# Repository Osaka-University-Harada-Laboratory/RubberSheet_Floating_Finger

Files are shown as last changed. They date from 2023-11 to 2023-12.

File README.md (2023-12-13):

# オープンソース版フローティングフィンガー（近接覚センサTK-01使用）

## 概要
- 3Dビジョンレスばら積みピッキングや突き指防止機能を持つ柔軟機構・センシングユニット．

- 具体的な組立手順はYouTubeに公開 ---> https://youtu.be/J7uZkjt3QmM

- 第24回計測自動制御学会システムインテグレーション部門講演会(SI2023)において発表．<br>
発表タイトル：**柔軟膜を用いたオープンソースなフローティングフィンガー機構**

<!-- ![Overview](/images/SI2023_fig_overview.png) -->


## パーツ
- ipt：inventor向けCADデータ (.ipt, .iam)
- step：STEPファイル (.stp)
- 組み立て後のデータ：RSFF_assembly_1_v3_clearance

### 近接覚センサ：TK-01
- 株式会社Thinker製の近接覚センサ"TK-01"を使用
- 以下から見積もり・購入が可能

  https://www.thinker-robotics.co.jp/contact

### センサケース
- 該当CADファイル：RSFF_cover_1_v3_clearance\
- 3Dプリンタで製作

<br><br>
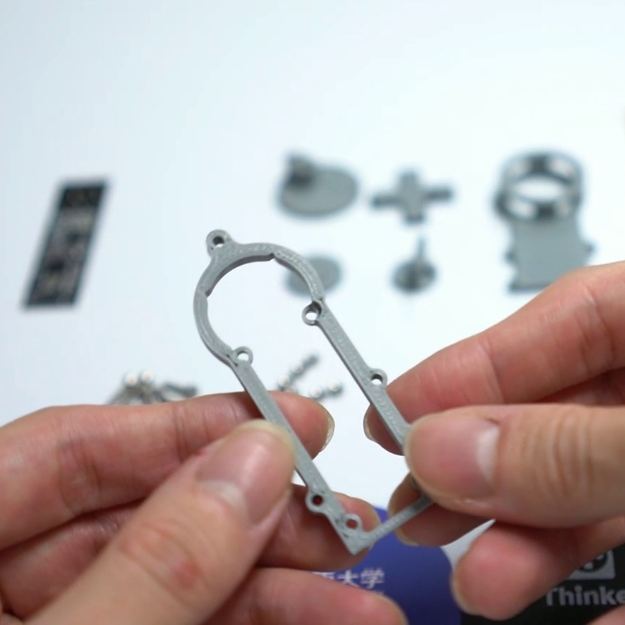
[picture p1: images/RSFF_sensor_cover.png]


### センサカバー
- 該当CADファイル：RSFF_cover_2_v2_clearance\
- 3Dプリンタで製作

<br><br>
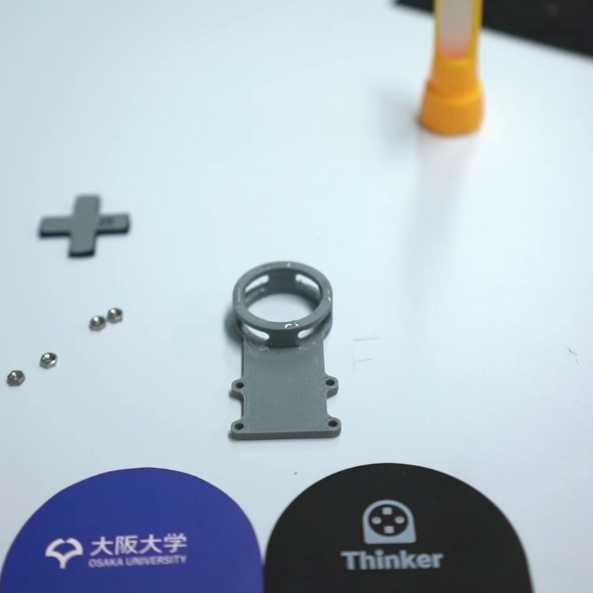
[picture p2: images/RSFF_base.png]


### 柔軟膜
- 該当CADファイル：RubberSheet_1
- 材料：市販の飴ゴムシート　[購入先リンク](https://www.monotaro.com/g/01013365/?t.q=%E9%A3%B4%E3%82%B4%E3%83%A0%E3%82%B7%E3%83%BC%E3%83%88)\
- 作成方法：RubberSheet_1を3Dプリンターで印刷したパーツをもとに切り取る
<br><br>
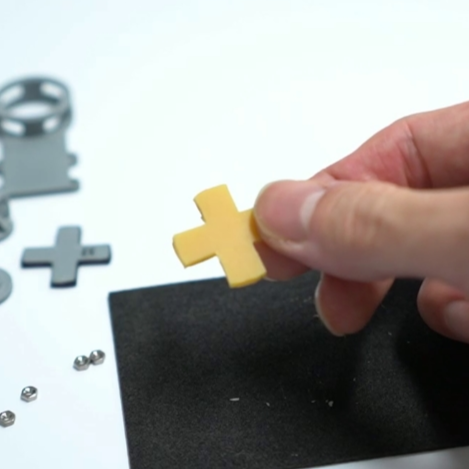
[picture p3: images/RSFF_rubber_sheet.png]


### 爪
- 該当CADファイル：RSFF_tip_metal_1\
- 素材：アルミニウム\
- 作成方法：meviyを利用し外注　[meviyリンク](https://meviy.misumi-ec.com/ja-jp/)
<br><br>


### 爪と柔軟膜の接続部分
- 該当CADファイル：RSFF_tip_mount_1\
- 作成方法：センサカバーと同じ
<br><br>
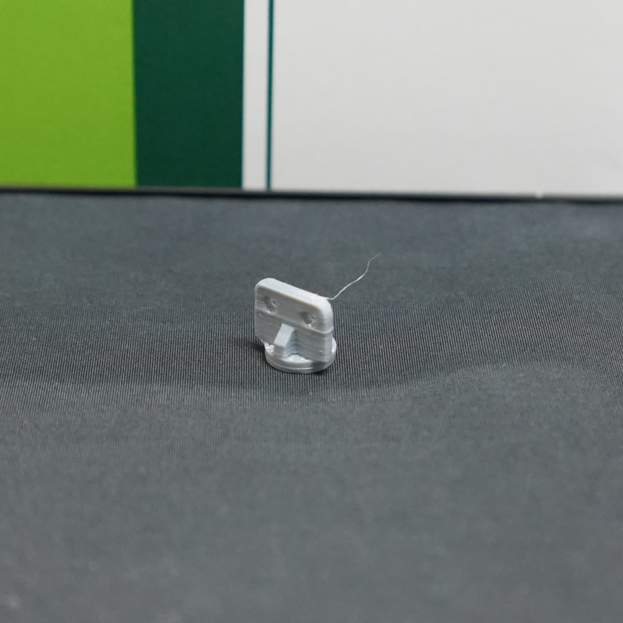
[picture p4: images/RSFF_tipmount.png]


### 反射板
- 該当CADファイル：RSFF_reflector_v2\
- 作成方法：センサカバーと同じ
<br><br>
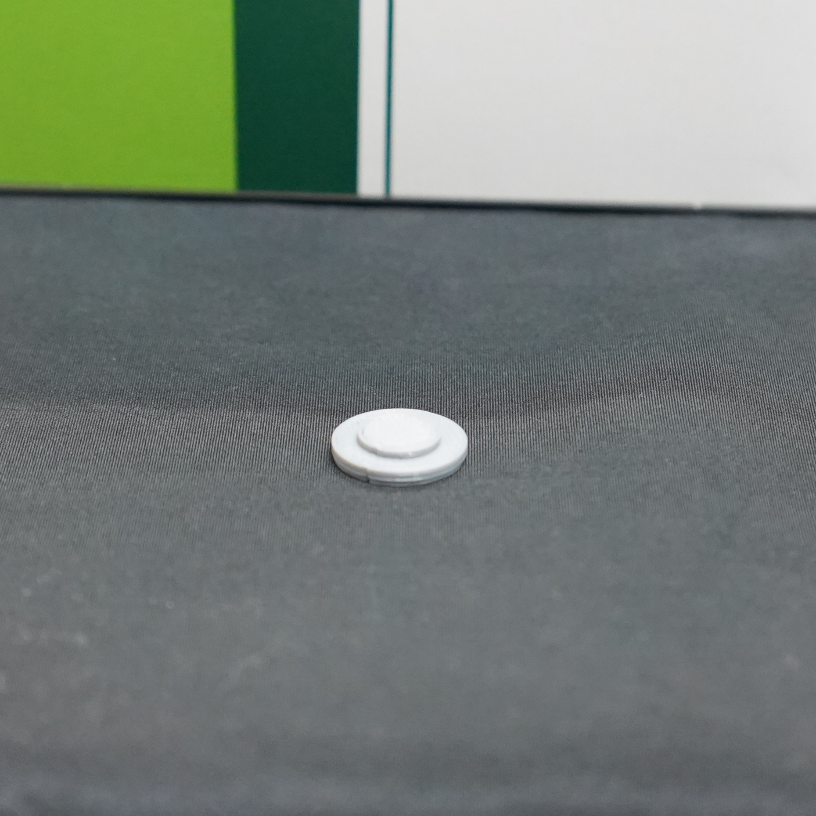
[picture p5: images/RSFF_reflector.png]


### COBOTTAの手先との接続部分
- 該当CADファイル：RSFF_mount_1_clearance, RSFF_mount_1_clearance_MIR1\
- 作成方法：センサカバーと同じ
<br><br>
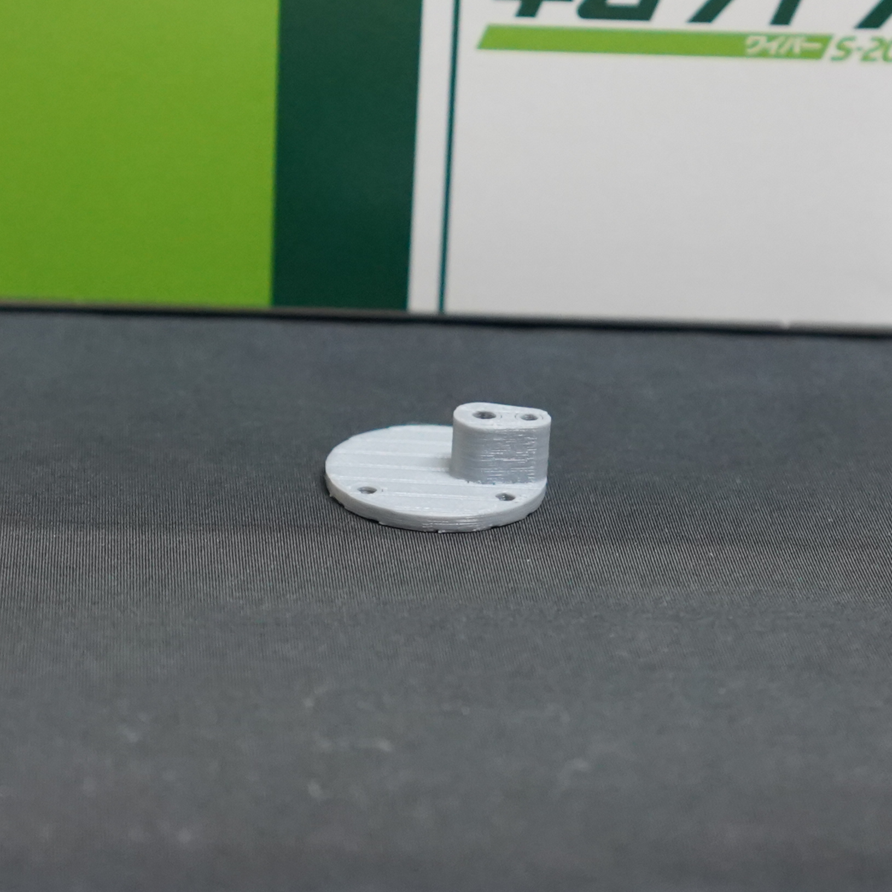
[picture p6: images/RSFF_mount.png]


## 道具・細かい部品
- ハサミ
- ボルト(M2×8：6個，M2×10：5個)
- ナット(M2)
- 瞬間接着剤（アロンアルファ，他種の接着剤では接着力が減少する場合があるので注意）
- 白い紙
- 低反射黒インク（「黒色無双」相当品）[購入先リンク](https://www.amazon.co.jp/dp/B08JYK85HP/?m=A3NCQXDSLN8VX8)\
- 筆

### 使用実績のある3Dプリンタ

研究室では以下の2種類の3Dプリンターで作成した実績あり．

  1. **光造形式3Dプリンター (AGILISTA-3200)**
     - モデル材：AR-M2
     - サポート材：AR-S1
  1. **FDM式3Dプリンター (Zortrax M200 Plus)**
     - フィラメント：Z-ULTRAT (ABS系樹脂)

## 構造図

- 具体的な組立手順はこちら ---> https://youtu.be/J7uZkjt3QmM

<!-- ![組み立て](/images/SI2023_fig_CAD_2.png) -->
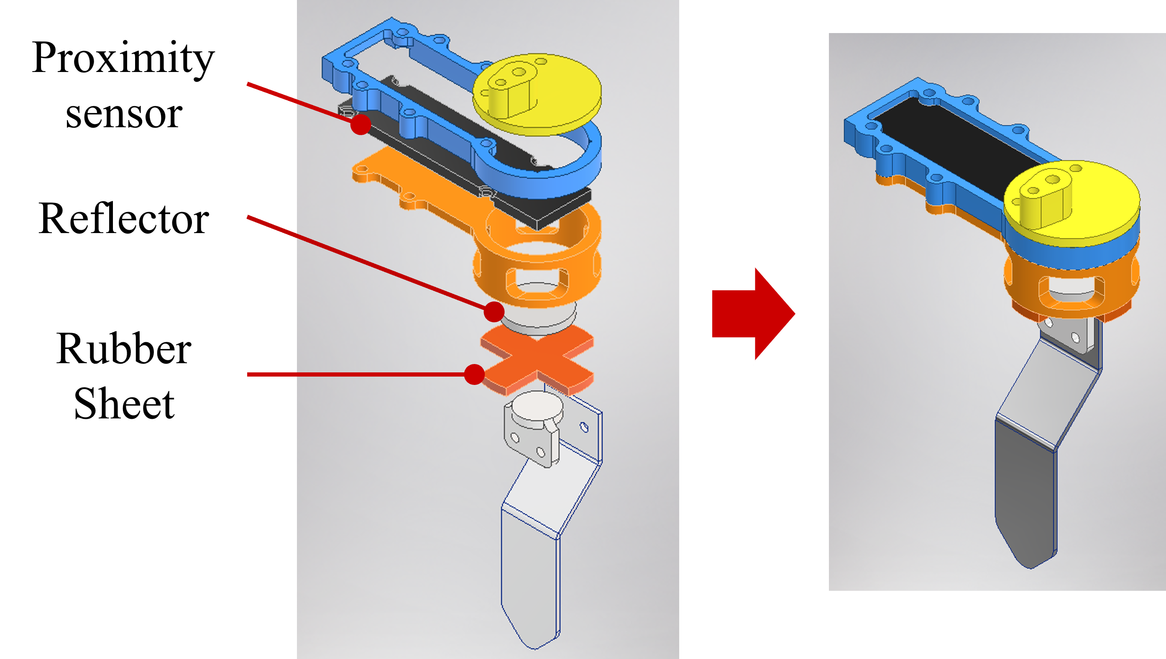
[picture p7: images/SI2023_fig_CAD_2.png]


## 備考
- センサカバーにはセンサ基板に対して約0.2mmのクリアランスを設けている．

## 謝辞
- 本研究は株式会社Thinkerとの共同研究の一環として実施された．

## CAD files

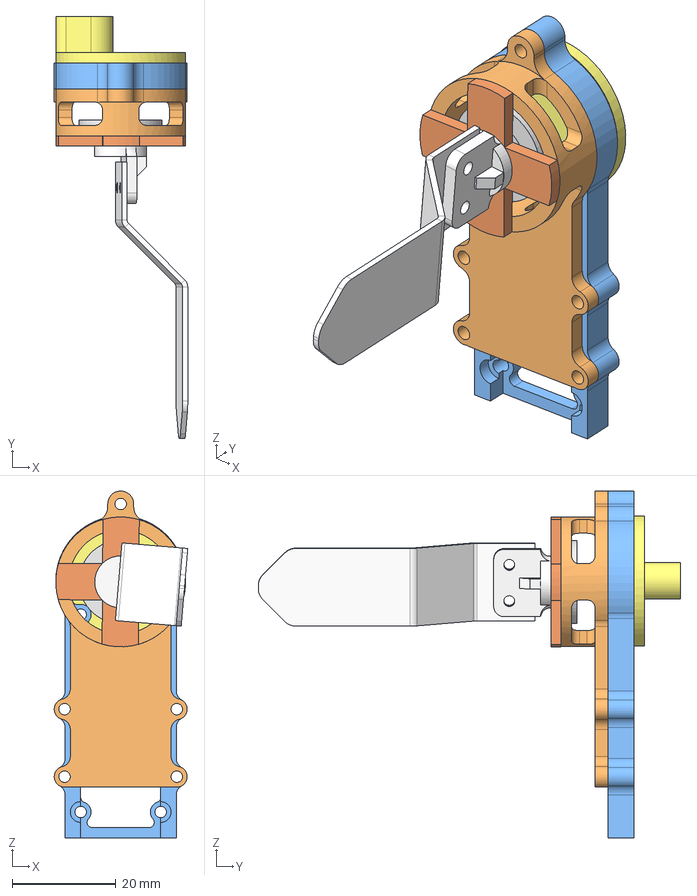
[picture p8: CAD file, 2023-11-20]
step/RSFF_assembly_1_v3_clearance.stp
25.7 x 81.3 x 66.8 mm
RSFF_cover_1_v3_clearance
RSFF_cover_2_v2_clearance
RSFF_tip_mount_1_clearance
RSFF_reflector_v2
RSFF_tip_mount_1
RubberSheet_1
RSFF_tip_metal_1

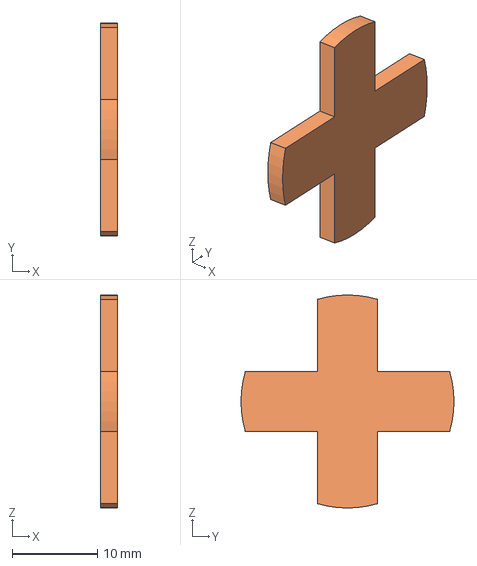
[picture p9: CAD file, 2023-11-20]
step/RubberSheet_1.stp
2.00 x 25.0 x 25.0 mm

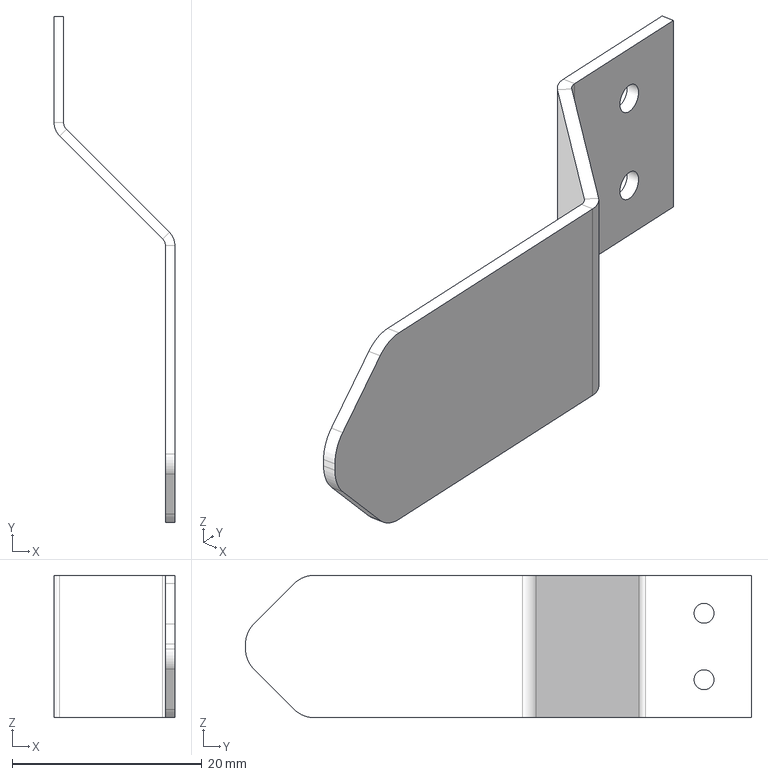
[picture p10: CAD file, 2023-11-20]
step/RSFF_tip_metal_1.stp
12.7 x 53.3 x 15.0 mm

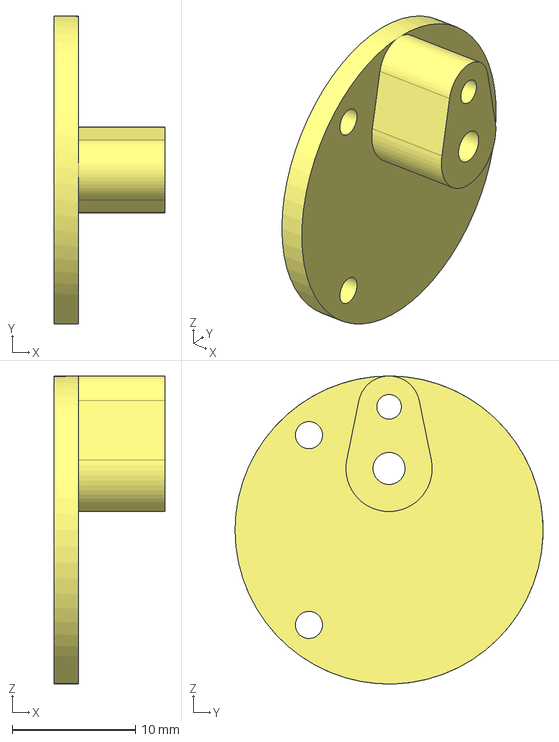
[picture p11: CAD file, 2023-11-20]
step/RSFF_mount_1_clearance_MIR1.stp
9.00 x 25.0 x 25.0 mm

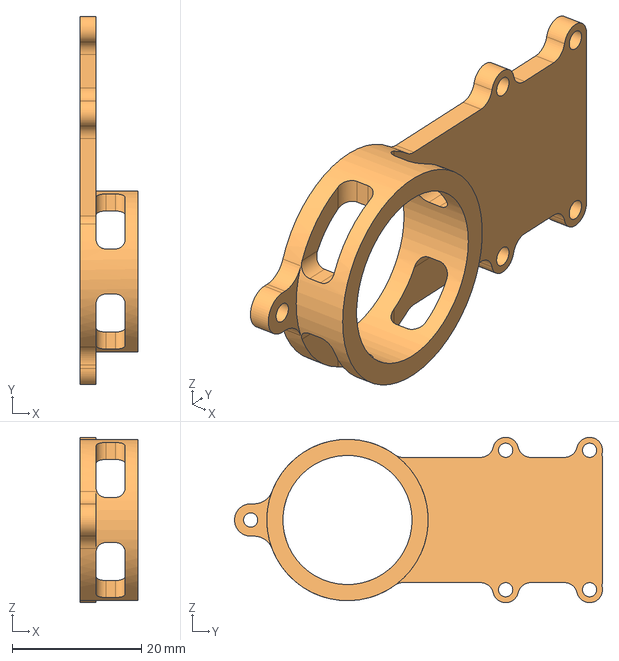
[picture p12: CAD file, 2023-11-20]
step/RSFF_cover_2_v2_clearance.stp
9.00 x 57.0 x 25.6 mm

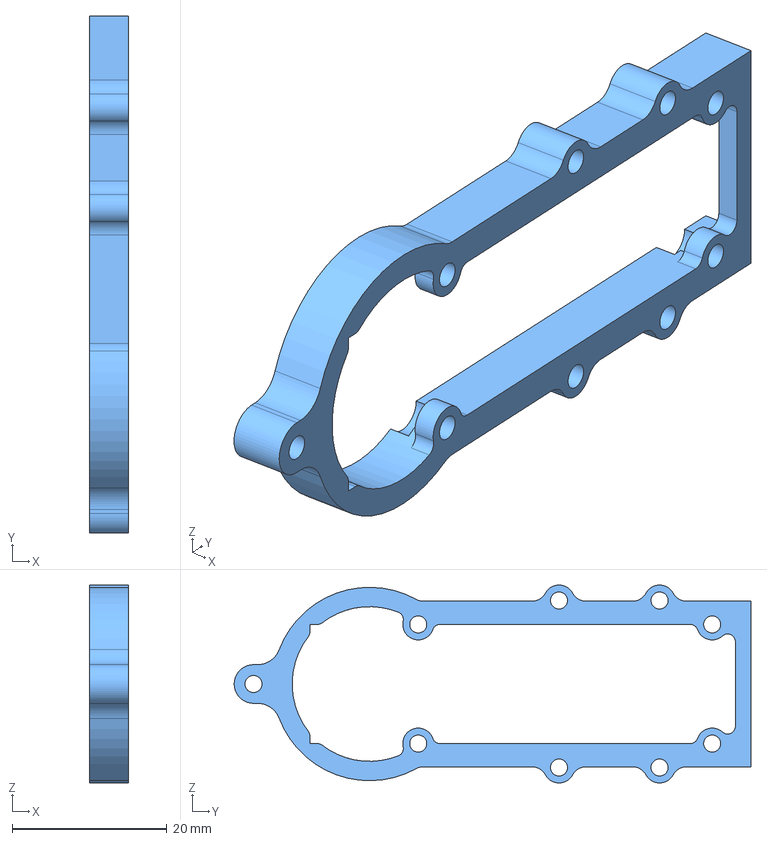
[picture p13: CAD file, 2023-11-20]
step/RSFF_cover_1_v3_clearance.stp
5.00 x 66.8 x 25.6 mm

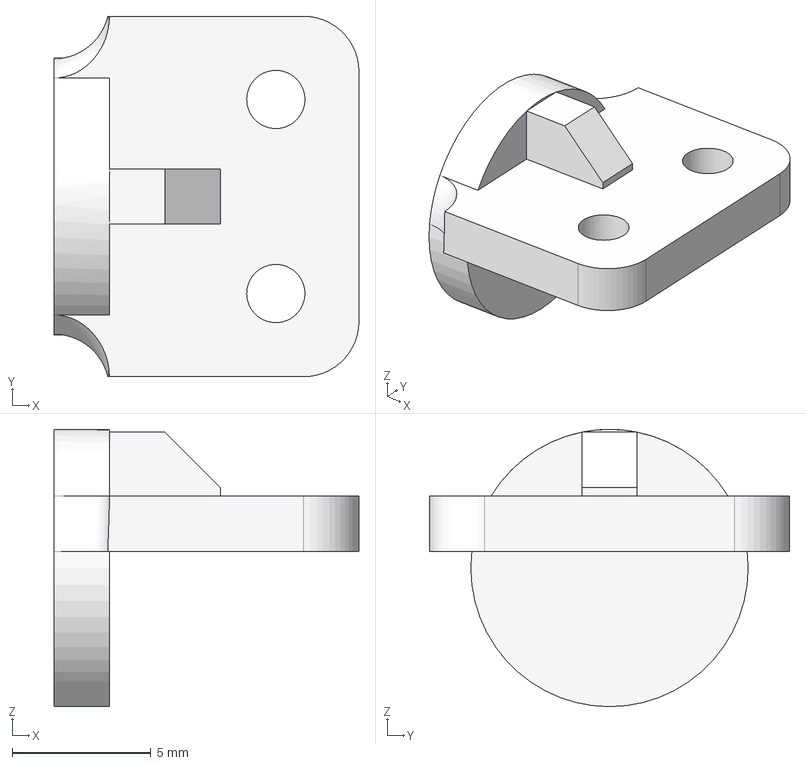
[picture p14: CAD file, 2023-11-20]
step/RSFF_tip_mount_1.stp
11.0 x 13.0 x 10.0 mm

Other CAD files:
step/RSFF_mount_1_clearance.stp
ipt/RSFF_assembly_1_v3_clearance.iam
ipt/RSFF_cover_1_v3_clearance.ipt
ipt/RSFF_cover_2_v2_clearance.ipt
ipt/RSFF_mount_1_clearance.ipt
ipt/RSFF_mount_1_clearance_MIR1.ipt
ipt/RSFF_reflector_v2.ipt
ipt/RSFF_tip_metal_1.ipt
ipt/RSFF_tip_mount_1.ipt
ipt/RubberSheet_1.ipt

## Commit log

2023-11-20 README修正
2023-11-20 パーツ詳細を追加
2023-11-20 図を追加
2023-11-20 画像をHTMLに書き換え
2023-11-20 画像を縮小，備考を追加
2023-11-20 CADデータ追加
    [RSFF_assembly_1_v3_clearance.iam, RSFF_assembly_1_v3_clearance.stp, RSFF_cover_1_v3_clearance.ipt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]
2023-12-03 画像を変更
2023-12-04 ライセンスファイル追加
2023-12-04 Update README.md
    パーツの説明修正
2023-12-06 パーツの写真追加
2023-12-06 READMEにパーツの写真を追加
2023-12-06 パーツ写真のサイズ変更
2023-12-06 写真位置変更
